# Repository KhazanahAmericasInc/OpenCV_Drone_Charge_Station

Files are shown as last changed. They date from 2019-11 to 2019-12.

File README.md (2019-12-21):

## Description  
An intelligent landing pad that can detect a drone flying overhead and take control to autonomously land the drone and recharge it. In this case, I am using an inexpensive indoor drone flown manually by a person before the autonomous landing procedure takes over control. In a commercial application, the drone would use other sensors to fly autonomous missions before the landing. I am focusing on just the landing portion of the problem.  

## Video  
YouTube Demo Video: https://www.youtube.com/watch?v=vQnh8SQZ9hY  

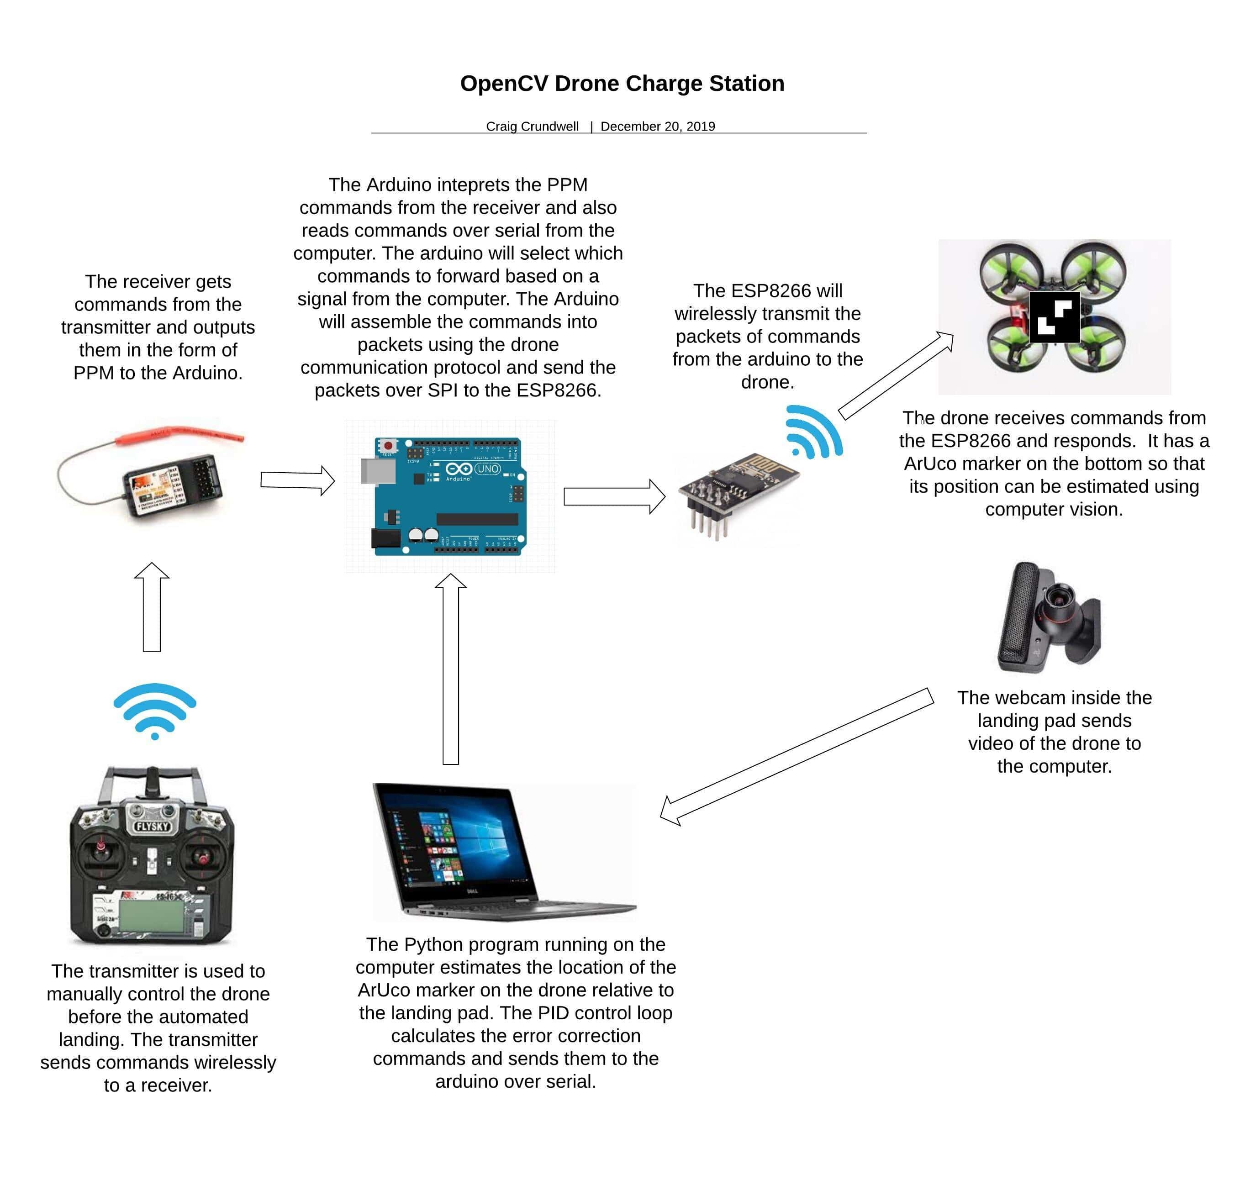
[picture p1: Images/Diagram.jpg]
Systems Diagram


To fly a drone autonomously, you need to know the actual location of the drone and a target location. Most advanced drones use GPS to accomplish this. For cheaper indoor drones, they have no sense of location so we need to provide this information to the control system.  We selected computer vision to track the drone position because it is inexpensive compared to other sensor options. The AruCo library is used to estimate the location of a small tag on the bottom of the drone. A webcam is located in the landing pad to view the drone flying above.  

Once we know the actual location of the drone and a desired location, we need to give the drone instructions to fly it autonomously. The system must calculate the appropriate commands to make the drone correct its position errors and try reach the target location. We can determine these commands using a PID control loop. A PID control loop has multiple values that can finely tune how the drone should respond to errors in it's location. The tuning of these values is critical for the drone to respond correctly without overshooting or causing other bad behavior like oscillations.  

For each axis of the drone's movement, there are 3 values to adjust; P, I, and D. The P value is proportional and represents how far the drone is from the target. If the drone is very far from the target, it must react strongly to bring it back to the target. The I value is integral and represents the past or historic error in the system. If the drone has been away from the target for a while, it must react strongly to try bring it back. D is for derivative and represents the current rate of change. If the drone is currently moving toward the target, less correction is required than if it is moving away from the target. PID values are different for every unique system. For example a more heavy and sluggish drone may need higher correction values to tune the flight vs a lighter and nimble drone. Even factors such as the frame rate of the camera will change the system response.  

In this project a Python program is used to read the video frames from the webcam and estimate the location of the drone. The program calculates the commands to send the drone to correct for errors when the drone drifts away from the target location. The Python program sends the commands over serial to a connected Arduino. The Arduino interprets these commands and assembles packets and transmits them to the drone using an Esp8266 module.  

Because we also need a way for the user to fly the drone before the landing pad takes control, there is a connected receiver to the Arduino that can forward commands from a user transmitter (controller). The Arduino can toggle between sending the commands from the computer, or commands from the users transmitter. This allows control of the drone to toggle between manual or autonomous flight.  

When the user flies the drone over the landing pad, the computer vision will detect the drone and the Python program tells the Arduino that it is taking over control. The Python program will set a target location and estimate the drone location. It will perform error calculations and send the drone commands to correct the position. When the Python program takes over control, the Arduino turns on the lights to allow the camera to more reliably track the drone location. The program hovers the drone for a few seconds to stabilize it before slowly lowering to the landing pad surface. Once the drone gets very close to the surface it experiences significantly increased lift called ground effect. The nearby ground increases the efficiency of the lift and causes the drone to bounce unless the throttle is dropped significantly. The PID loop is unable to handle this new system response so it fails to land the drone smoothly at this height. Instead, the throttle is lowered significantly for a short while before being turned off. This allows for a smoother landing.  

Once the drone has landed on the pad, it needs to doc with the charger. The drone is given gentle throttle and backward command so it slides backward and is physically guided into the charging dock. Magnets connect with small wires on the drone to transfer power and charge the battery.  

The Arduino can read the state of an LED on the charger which indicates if the it is still charging. The Arduino will fade the LED lights to indicate that the drone is charging. The charge is done when the lights turn off.  

When the charging is finished, the user can toggle a switch to make the landing pad physically disconnect the drone from the magnets and allow the drone to take off. The user performs the take off because it is difficult for an inexperienced user to take control of a drone already in flight. The reaction for adjusting the throttle must be very quick to prevent the drone from dropping of climbing too rapidly. Because of this, the computer has no problem reacting to taking control from a user smoothly but the reverse is challenging for the user.  

## Hardware
- Eachine E010 quadcopter 
- Arduino Uno 
- 2.4GHz nRF24L01+ 
- PlayStation Eye webcam  
- Flysky i6 transmitter 
- Flysky PPM compatible receiver  
- 12V power supply  
- 12V to 5V voltage converter 
- Windows 10 laptop

## Software
- Python 3.6 32bit  
- OpenCV contrib 4.1.2 
- Arduino 1.8.10
- CL Eye Driver 5.3.0.0341
- CL Eye Platform SDK 1.6.4.0028  

## Credit  
- Rotation matrix to euler angles math: https://www.learnopencv.com/rotation-matrix-to-euler-angles/   
- Inspiration and PID loop framework from @partomatl: https://github.com/partomatl   
- Signal filtering from @partomatl : https://github.com/partomatl   
- Transmitter protocol from goebish on RCgroups / github: https://github.com/goebish/nrf24_multipro  
- Serial communication modification of transmitter protocol from @perrytsao:  https://github.com/perrytsao  
- The PPM library @Nikkilae: https://github.com/Nikkilae/PPM-reader  

## TroubleShooting 
- A driver and SDK is required to run the play station camera on windows. The SDK package includes a test program which is useful to test the connection to the camera. Sometimes the camera needs to be moved to a different USB port and re selected in the test program to function properly. If the landing base does not react to the drone flying overhead, test the connection with the test program. 
- Avoid using the base with bright lights directly overhead as they can make it more difficult for the camera to detect the drone 
- Make sure the Aruco tracker on the bottom of the drone is not significantly bent or worn away. Replace it with a fresh one if required. 
- If the drone drifts a bit and does not fly level, the small trims buttons can be used to adjust for level flight  
- If the drone drifts significantly during flight, place it on a level surface and move both sticks to the bottom middle to re calibrate the on board sensors   
- If the system is drastically changed, the PID values may need to be tuned again. Start with the last known working values and adjust each P, I, or D value up or down slightly and monitor the system response. The pitch and roll can be tuned together if the system response is the same on both axis's (for a square drone it is usually the same). For common systems like the flight controller for a drone, the tuning process is well documented and online help can provide some rules of thumb to help speed up the process. For a less known system like this project the tuning is more guess and check. It is slow and frustrating but currently it is the only way.

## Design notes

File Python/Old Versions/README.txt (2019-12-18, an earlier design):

These programs were used to develop functinality. 
They are no longer compatabile with the the current arduino code versions

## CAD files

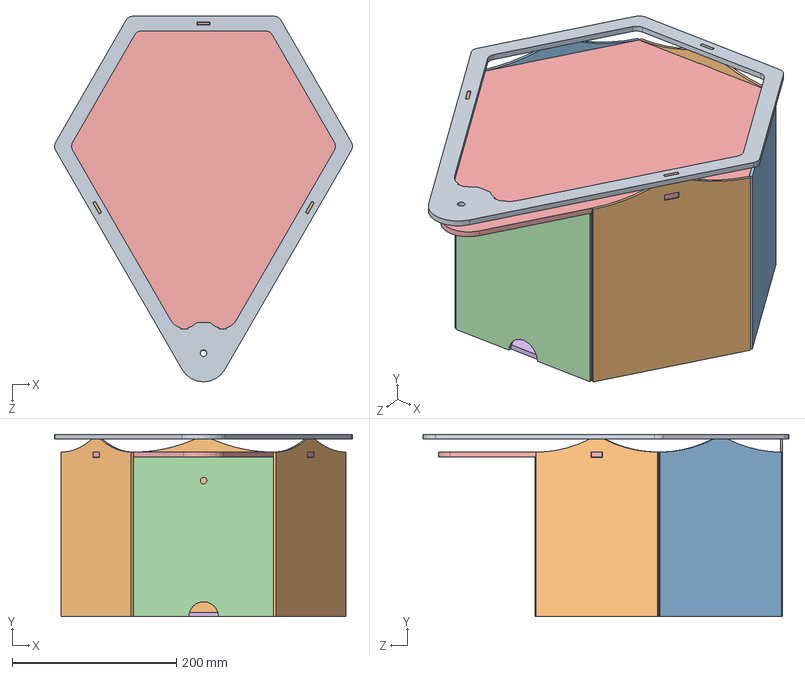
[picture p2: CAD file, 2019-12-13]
Solidworks/Hexagon base v1/Base_v1.SLDASM
362.5 x 221.5 x 444.9 mm
Top_v1
Side_v1 connect x 3
Side_v1 basic x 2
Side_v1 rear
pad_v1
Bottom_v1

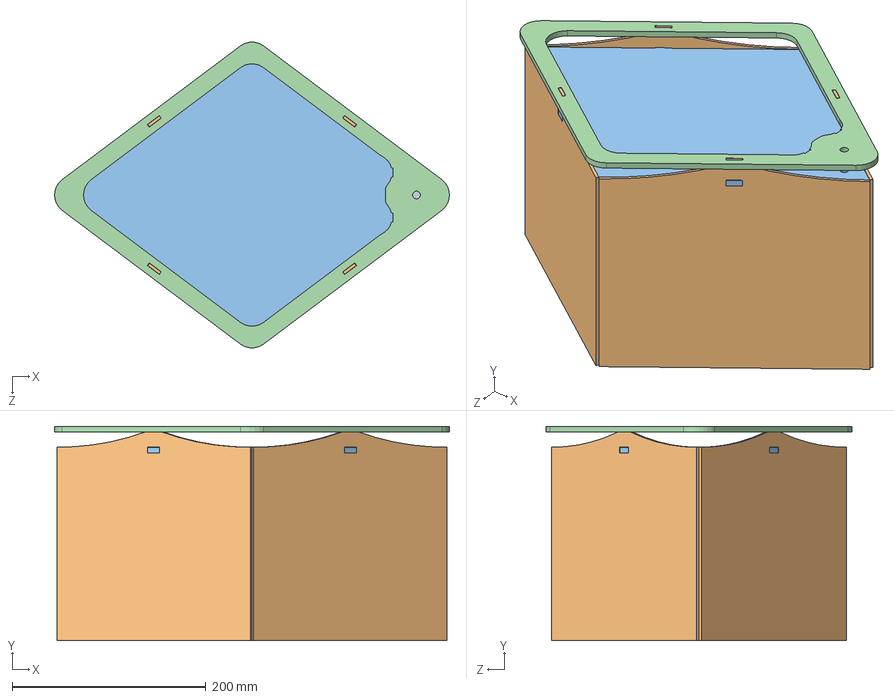
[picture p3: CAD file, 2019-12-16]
Solidworks/Diamond base v1/diamond_base_v1.SLDASM
408.2 x 221.5 x 315.9 mm
diamond_bottom_v1
diamond_side_v1 x 4
diamond_pad_v1
diamond_top_v1
diamond_middle_v1

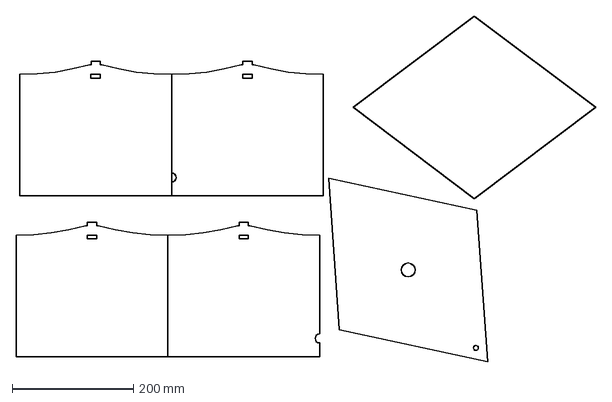
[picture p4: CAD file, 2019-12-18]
Solidworks/Diamond base v1/thin_black_cut_v1.dxf
954.8 x 568.7 mm

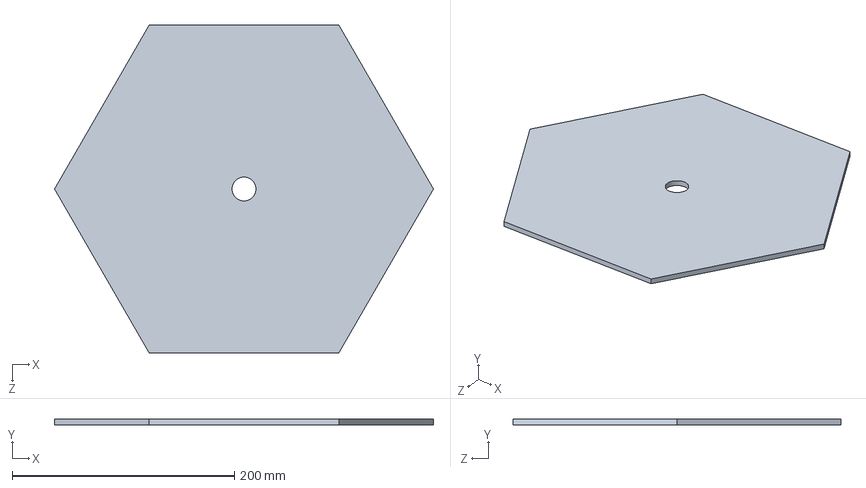
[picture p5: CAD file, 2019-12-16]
Solidworks/Hexagon base v1/middle_v1.SLDPRT
341.0 x 5.00 x 295.3 mm

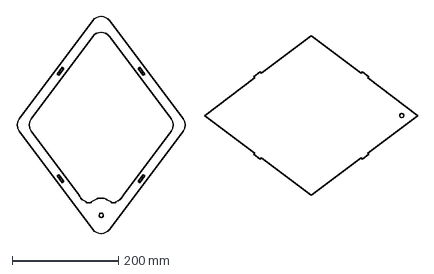
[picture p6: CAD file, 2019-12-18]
Solidworks/Diamond base v1/Thick_clear_cut_v1.dxf
754.3 x 408.3 mm

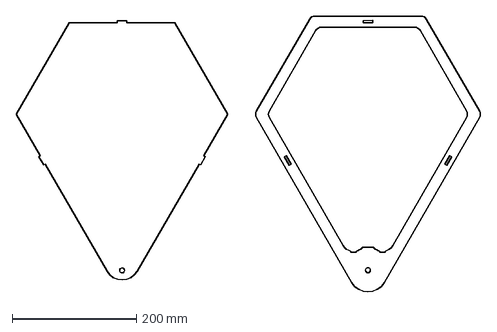
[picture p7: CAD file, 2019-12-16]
Solidworks/Hexagon base v1/Thick Clear Cut.dxf
748.7 x 444.9 mm

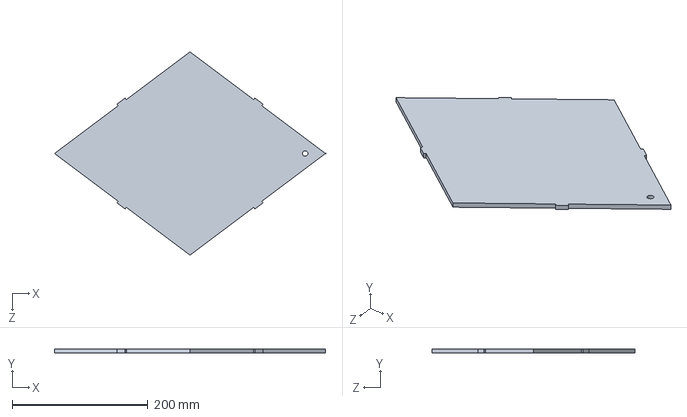
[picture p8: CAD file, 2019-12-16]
Solidworks/Diamond base v1/diamond_pad_v1.SLDPRT
400.0 x 5.63 x 300.0 mm

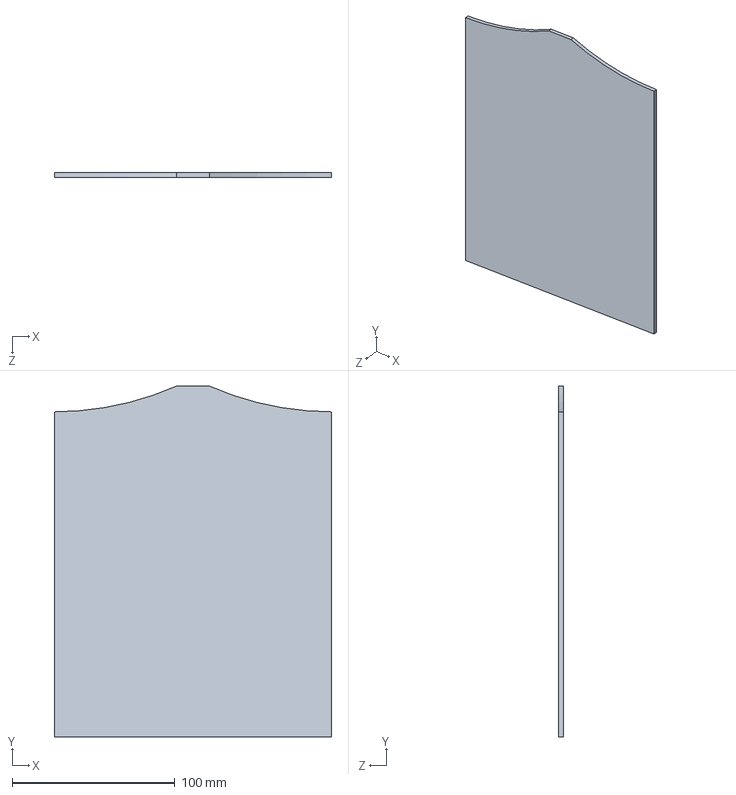
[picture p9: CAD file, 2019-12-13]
Solidworks/Hexagon base v1/Side_v1 basic.SLDPRT
170.5 x 215.9 x 2.95 mm

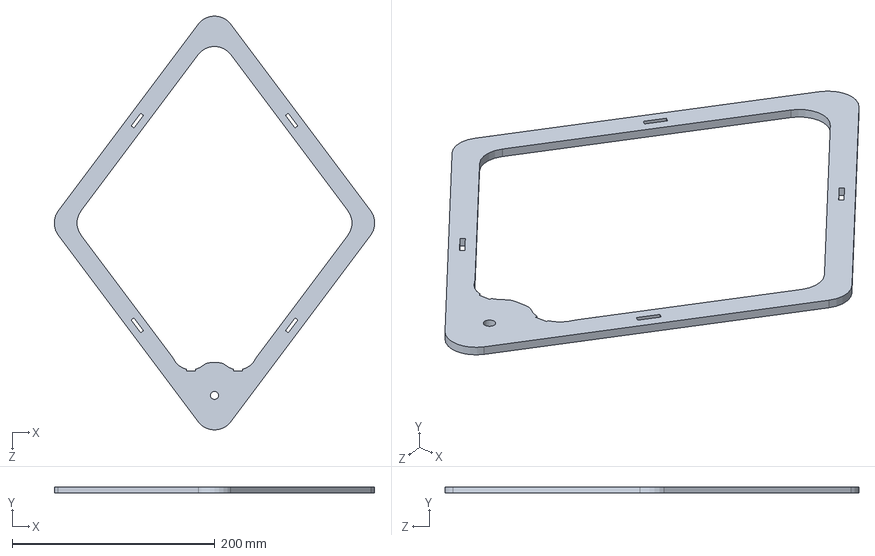
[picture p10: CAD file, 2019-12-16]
Solidworks/Diamond base v1/diamond_top_v1.SLDPRT
315.9 x 5.63 x 408.2 mm

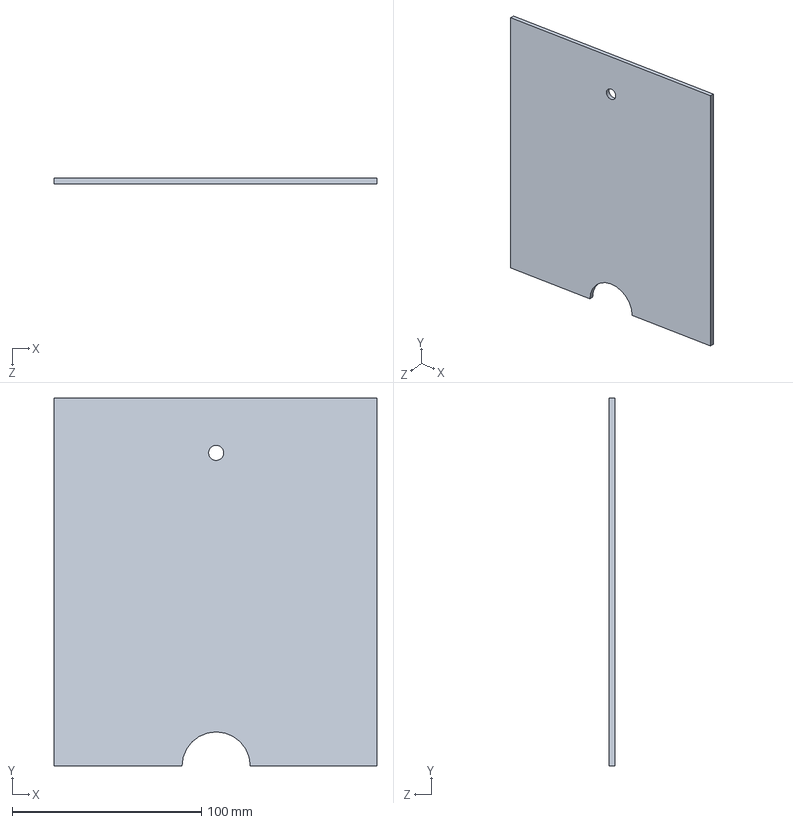
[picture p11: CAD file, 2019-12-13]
Solidworks/Hexagon base v1/Side_v1 rear.SLDPRT
170.5 x 194.3 x 2.95 mm

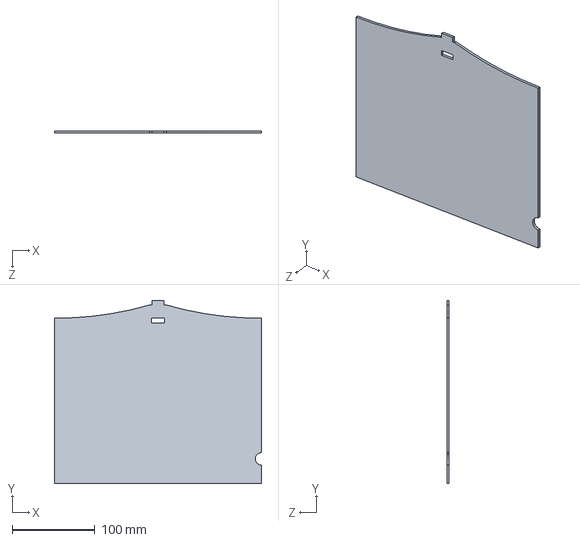
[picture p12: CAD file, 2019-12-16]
Solidworks/Diamond base v1/diamond_side_back_v1.SLDPRT
250.0 x 221.5 x 2.95 mm

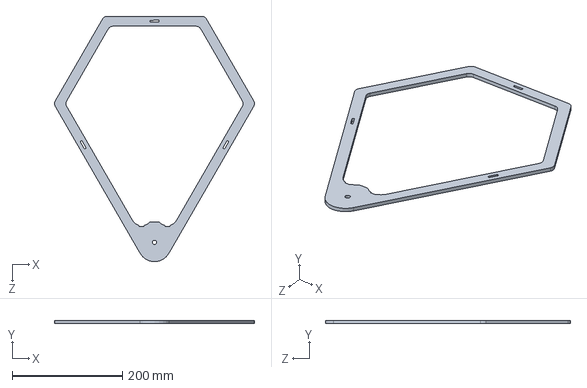
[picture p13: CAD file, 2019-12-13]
Solidworks/Hexagon base v1/Top_v1.SLDPRT
362.5 x 5.63 x 444.9 mm

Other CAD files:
Solidworks/Hexagon base v1/Thin Black Cut.dwg
Solidworks/Diamond base v1/diamond_middle_v1.SLDPRT
Solidworks/Hexagon base v1/Side_v1 connect.SLDPRT
Solidworks/Diamond base v1/diamond_bottom_v1.SLDPRT
Solidworks/Diamond base v1/diamond_side_v1.SLDPRT
Solidworks/Hexagon base v1/Bottom_v1.SLDPRT
Solidworks/Diamond base v1/Thick_clear_cut_v1.dwg
Solidworks/Diamond base v1/diamond_bottom_v1.DWG
Solidworks/Diamond base v1/diamond_middle_v1.DWG
Solidworks/Diamond base v1/diamond_pad_v1.DWG
Solidworks/Diamond base v1/diamond_side_back_v1.DWG
Solidworks/Diamond base v1/diamond_side_v1.DWG
Solidworks/Diamond base v1/diamond_top_v1.DWG
Solidworks/Diamond base v1/thin_black_cut_v1.dwg
Solidworks/Hexagon base v1/Bottom_v1.DWG
Solidworks/Hexagon base v1/Side_v1 basic.DWG
Solidworks/Hexagon base v1/Side_v1 connect.DWG
Solidworks/Hexagon base v1/Side_v1 rear.DWG
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

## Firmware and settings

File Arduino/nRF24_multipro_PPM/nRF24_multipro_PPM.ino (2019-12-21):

/*
 ******************************************************************************
 This is a fork of the Multi-Protocol nRF24L01 Tx project
 from goebish on RCgroups / github. 
 This serial communication of this program is from perrytsao on github.com
 The PPM library is from: https://github.com/Nikkilae/PPM-reader
 
 This version accepts either PPM or serial port strings and converts
 them to ppm commands which are then transmitted via
 the nRF24L01.
 The purpose of this code is to enable control over the Eachine E010 
 drone via code running on a PC or a FS-iA6B reciever connected via PPM. 

 This code reads channel values over serial from a Python program. 
 The first 4 channels are for control of the drone. The 5th channel selects 
 if the channel values from the python program should be sent to the drone 
 or if the channel values from the PPM of the attached receiver should be sent

 This code was tested on the Arduino Uno and nRF24L01 module.

 *********************************************************************************

 ##########################################
 #####   MultiProtocol nRF24L01 Tx   ######
 ##########################################
 #        by goebish on rcgroups          #
 #                                        #
 #   Parts of this project are derived    #
 #     from existing work, thanks to:     #
 #                                        #
 #   - PhracturedBlue for DeviationTX     #
 #   - victzh for XN297 emulation layer   #
 #   - Hasi for Arduino PPM decoder       #
 #   - hexfet, midelic, closedsink ...    #
 ##########################################


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
 You should have received a copy of the GNU General Public License.
 If not, see <http://www.gnu.org/licenses/>.
 */

#include <util/atomic.h>
#include <EEPROM.h>
#include "iface_nrf24l01.h"
#include <string.h>
#include <PPMReader.h>

//Used to control the servos
#include <Servo.h>

//PPM input on pin 2
int interruptPin = 2;

//Amount of channels to read from PPM
int channelAmount = 5;

//Initialize the ppm reader
PPMReader ppm(interruptPin, channelAmount);

int control = 1000;//Track control (1000 is user control, 2000 is computer control)
int triggerDetach = 0; //Toggle for charge detach
int lightMode = 0; //of for off, 1 for on, 3 for fade
int aux = 1000; //Used to record aux channel from user controller

//These values are used to average the voltage readings from the charger led
const int numReadings = 10;
int readings[numReadings];      // the readings from the analog input
int readIndex = 0;              // the index of the current reading
int total = 0;                  // the running total
int average = 0;                // the average

float brightness = 0;    // how bright the LED is
float fadeAmount = 0.3;    // how many points to fade the LED by

//Tracks timing of events
unsigned long lastString = 0;
unsigned long currentTime = 0;
unsigned long ElapsedTime = 0;

// ############ Wiring ################
//SPI Comm.pins with nRF24L01
#define MOSI_pin  3  // MOSI - D3
#define SCK_pin   4  // SCK  - D4
#define CE_pin    5  // CE   - D5
#define MISO_pin  A0 // MISO - A0
#define CS_pin    A1 // CS   - A1
#define landingLightPin 11 // the PWM pin the LED is attached to
#define ledPin    13 // LED  - D13
#define servoPin 6
#define chargePin A5

// SPI outputs
#define MOSI_on PORTD |= _BV(3)  // PD3
#define MOSI_off PORTD &= ~_BV(3)// PD3
#define SCK_on PORTD |= _BV(4)   // PD4
#define SCK_off PORTD &= ~_BV(4) // PD4
#define CE_on PORTD |= _BV(5)    // PD5
#define CE_off PORTD &= ~_BV(5)  // PD5
#define CS_on PORTC |= _BV(1)    // PC1
#define CS_off PORTC &= ~_BV(1)  // PC1
// SPI input
#define  MISO_on (PINC & _BV(0)) // PC0

#define RF_POWER TX_POWER_80mW

// PPM stream settings
#define CHANNELS 5 // number of channels in ppm stream, 12 ideally
enum chan_order{
    THROTTLE,
    AILERON,
    ELEVATOR,
    RUDDER,
    AUX1,  // (CH5)  led light, or 3 pos. rate on CX-10, H7, or inverted flight on H101
    AUX2,  // (CH6)  flip control
    AUX3,  // (CH7)  still camera (snapshot)
    AUX4,  // (CH8)  video camera
    AUX5,  // (CH9)  headless
    AUX6,  // (CH10) calibrate Y (V2x2), pitch trim (H7), RTH (Bayang, H20), 360deg flip mode (H8-3D, H22)
    AUX7,  // (CH11) calibrate X (V2x2), roll trim (H7)
    AUX8,  // (CH12) Reset / Rebind
};

//Define channel values 
#define PPM_MIN 1000
#define PPM_SAFE_THROTTLE 1050
#define PPM_MID 1500
#define PPM_MAX 2000
#define PPM_MIN_COMMAND 1300
#define PPM_MAX_COMMAND 1700
#define GET_FLAG(ch, mask) (ppm2[ch] > PPM_MAX_COMMAND ? mask : 0)
#define GET_FLAG_INV(ch, mask) (ppm2[ch] < PPM_MIN_COMMAND ? mask : 0)

// supported protocols
enum {
    PROTO_V2X2 = 0,     // WLToys V2x2, JXD JD38x, JD39x, JJRC H6C, Yizhan Tarantula X6 ...
    PROTO_CG023,        // EAchine CG023, CG032, 3D X4
    PROTO_CX10_BLUE,    // Cheerson CX-10 blue board, newer red board, CX-10A, CX-10C, Floureon FX-10, CX-Stars (todo: add DM007 variant)
    PROTO_CX10_GREEN,   // Cheerson CX-10 green board
    PROTO_H7,           // EAchine H7, MoonTop M99xx
    PROTO_BAYANG,       // EAchine H8(C) mini, H10, BayangToys X6, X7, X9, JJRC JJ850, Floureon H101
    PROTO_SYMAX5C1,     // Syma X5C-1 (not older X5C), X11, X11C, X12
    PROTO_YD829,        // YD-829, YD-829C, YD-822 ...
    PROTO_H8_3D,        // EAchine H8 mini 3D, JJRC H20, H22
    PROTO_MJX,          // MJX X600 (can be changed to Weilihua WLH08, X800 or H26D)
    PROTO_SYMAXOLD,     // Syma X5C, X2
    PROTO_HISKY,        // HiSky RXs, HFP80, HCP80/100, FBL70/80/90/100, FF120, HMX120, WLToys v933/944/955 ...
    PROTO_KN,           // KN (WLToys variant) V930/931/939/966/977/988
    PROTO_YD717,        // Cheerson CX-10 red (older version)/CX11/CX205/CX30, JXD389/390/391/393, SH6057/6043/6044/6046/6047, FY326Q7, WLToys v252 Pro/v343, XinXun X28/X30/X33/X39/X40
    PROTO_FQ777124,     // FQ777-124 pocket drone
    PROTO_E010,         // EAchine E010, NiHui NH-010, JJRC H36 mini
    PROTO_END
};

// EEPROM locationss
enum{
    ee_PROTOCOL_ID = 0,
    ee_TXID0,
    ee_TXID1,
    ee_TXID2,
    ee_TXID3
};

uint16_t overrun_cnt=0;
uint8_t transmitterID[4];
uint8_t current_protocol;
static volatile bool ppm_ok = false;
uint8_t packet[32];
static bool reset=true;
volatile uint16_t Servo_data[12];
static uint16_t ppm2[12] = {PPM_MIN,PPM_MID,PPM_MID,PPM_MID,PPM_MIN,PPM_MIN,
                           PPM_MIN,PPM_MID,PPM_MID,PPM_MID,PPM_MID,PPM_MID,};
                           
//Sets channels to safe values                          
int throttle = 1000;
int aileron, elevator, rudder = 1500;

String inputString = "";         // a string to hold incoming data
boolean stringComplete = false;  // whether the string is complete
char *p, *i;
char* c = new char[200 + 1]; // match 200 characters reserved for inputString later
char* errpt;
uint8_t ppm_cnt;

//Creates servo object
Servo servo;

void setup()
{
    
    randomSeed((analogRead(A4) & 0x1F) | (analogRead(A5) << 5));
    
    //Sets pinModes
    pinMode(servoPin, OUTPUT);
    pinMode(MOSI_pin, OUTPUT);
    pinMode(SCK_pin, OUTPUT);
    pinMode(CS_pin, OUTPUT);
    pinMode(CE_pin, OUTPUT);
    pinMode(MISO_pin, INPUT);

    TCCR1A = 0;  //reset timer1
    TCCR1B = 0;
    TCCR1B |= (1 << CS11);  //set timer1 to increment every 1 us @ 8MHz, 0.5 us @16MHz
    set_txid(false);

    // Serial port input/output setup
    Serial.begin(115200);
    
    // reserve 200 bytes for the inputString:
    inputString.reserve(200);

    //Attach servo and set it to a safe position
    servo.attach(servoPin);
    servo.write(0);
    delay(400);
    servo.detach(); //Detach prevents jitter when it is not in use

    //Initializes reading values to 0
    for (int thisReading = 0; thisReading < numReadings; thisReading++) {
    readings[thisReading] = 0;
    }
}

void loop()
{
    
    // reset / rebind
    uint32_t timeout=0;
    if(reset || ppm2[AUX8] > PPM_MAX_COMMAND) {
        reset = false;
        Serial.println("selecting protocol");
        selectProtocol();
        Serial.println("selected protocol.");
        NRF24L01_Reset();
        Serial.println("nrf24l01 reset.");
        NRF24L01_Initialize();
        Serial.println("nrf24l01 init.");
        init_protocol();
        Serial.println("init protocol complete.");
    }
    
    // process protocol
    switch(current_protocol) {
        case PROTO_E010:
            timeout = process_MJX();
            break;     
    }
    
    overrun_cnt=0;

    //Track timing 
    currentTime = millis();
    
    if (stringComplete) {
        // process string

       //record timing of string received 
       lastString = millis();
        
       strcpy(c, inputString.c_str());
       p = strtok_r(c,",",&i); // returns substring up to first "," delimiter
       ppm_cnt=0;
       while (p !=0){
         int val=strtol(p, &errpt, 10);
         if (!*errpt) {
           if (ppm_cnt == 4) //command #5 (cnt is 4) is the control value
           {
              control = val;
           }  
           else
           {
              //Record commands in array
              ppm2[ppm_cnt]=val;
           }
           
           }
           p = strtok_r(NULL,",",&i);
           ppm_cnt+=1;
         }

 
         // clear the string:
         inputString = "";
         stringComplete = false;
     }

     // Read the string from the serial buffer
     while (Serial.available()) {
       // get the new byte:
       char inChar = (char)Serial.read();
       // if the incoming character is a newline, set a flag
       // so the main loop can do something about it:
       if (inChar == '\n') {
         stringComplete = true;
       }
       else {
         // add it to the inputString:
         inputString += inChar;
       }
     }
     
    if (control == 1000) //Overwrite serial channels with signal from PPM
    {     
        
        lightMode = 0; //Light off
        ppm2[0] = ppm.latestValidChannelValue(3, 0);
        ppm2[1] = ppm.latestValidChannelValue(1, 0);
        ppm2[2] = ppm.latestValidChannelValue(2, 0);
        ppm2[3] = ppm.latestValidChannelValue(4, 0);
        aux = ppm.latestValidChannelValue(5, 0);
        servo.attach(servoPin); //Attach servo to be used by the user
    }

    if (control == 2000) //Accept serial channels 
    {
      lightMode = 1; //Light on
      servo.detach(); //Detach servo to prevent jitter
    }
    
    //Set aux channels to middle levels to keep flip and headless modes off
    ppm2[4] = 1500;
    ppm2[5] = 1500;

    //Calculate time since last string is received 
    ElapsedTime = currentTime - lastString;

    //If connection is lost with the python program, send safe commands to the drone 
    if (ElapsedTime >= 500)
    {
      ppm2[0] = 1000;
      ppm2[1] = 1500;
      ppm2[2] = 1500;
      ppm2[3] = 1500;
    }

    // subtract the last reading:
    total = total - readings[readIndex];
    // read from the sensor:
    readings[readIndex] = analogRead(chargePin);
    // add the reading to the total:
    total = total + readings[readIndex];
    // advance to the next position in the array:
    readIndex = readIndex + 1;
  
    // if we're at the end of the array...
    if (readIndex >= numReadings) {
      // ...wrap around to the beginning:
      readIndex = 0;
    }

    // calculate the average:
    average = total / numReadings;

    //If user toggles the aux 5 switch, move the servo
    if ((triggerDetach == 0) && (aux <= 1500))
    {
      ppm2[0] = 1000;
      servo.write(120);
      triggerDetach = 1; 
    }

    //If user toggles the aux 5 switch, move the servo
    if ((control==1000) && (triggerDetach == 1) && (aux >= 1500))
    {
      servo.write(0);
      triggerDetach = 0;
    }

    //If charging is detected, fade the leds
    if (average >= 800)
    {
      lightMode = 3; 
    }

    //Turn off leds
    if (lightMode == 0)
    {
      analogWrite(landingLightPin, 0);
    }

    //Turn on leds
    else if (lightMode == 1)
    {
      analogWrite(landingLightPin, 255);
    }

    //Fade leds
    else if (lightMode == 3)
    {
      // change the brightness for next time through the loop:
      brightness = brightness + fadeAmount;
  
      // reverse the direction of the fading at the ends of the fade:
      if (brightness <= 0 || brightness >= 150) {
        fadeAmount = -fadeAmount;
        }

      analogWrite(landingLightPin, (int)brightness); //Write value to led in
    }
       
    // wait before sending next packet
    while(micros() < timeout) // timeout for CX-10 blue = 6000microseconds.
    {
      // overrun_cnt+=1;
      };
}

//Sets the transmitter ID
void set_txid(bool renew)
{
    uint8_t i;
    for(i=0; i<4; i++)
        transmitterID[i] = EEPROM.read(ee_TXID0+i);
    if(renew || (transmitterID[0]==0xFF && transmitterID[1]==0x0FF)) {
        for(i=0; i<4; i++) {
            transmitterID[i] = random() & 0xFF;
            EEPROM.update(ee_TXID0+i, transmitterID[i]);
        }
    }
}


//Selects the communication protocol
void selectProtocol()
{
    // Modified and commented out lines so that Cheerson CX-10 Blue is always selected
    // wait for multiple complete ppm frames
    ppm_ok = false;

    current_protocol = PROTO_E010; // EAchine E010, NiHui NH-010, JJRC H36 mini
    
    // update eeprom
    EEPROM.update(ee_PROTOCOL_ID, current_protocol);
    // wait for safe throttle
}

//Initializes the communication protocol
void init_protocol()
{
    switch(current_protocol) {
        case PROTO_E010:
            MJX_init();
            MJX_bind();
            break;
    }
}


      
      

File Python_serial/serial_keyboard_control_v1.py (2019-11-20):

import serial
import time, keyboard

def clamp(n, minn, maxn):
    if n < minn:
        return minn
    elif n > maxn:
        return maxn
    else:
        return n


throttle_rate=15
aileron_rate=400
elevator_rate=400
rudder_rate=300

# define middle PPM values that make the drone hover
throttle_middle = 1600  # up (+) and down (-)
aileron_middle = 1500  # left (-) and right (+)
elevator_middle = 1500  # forward (+) and backward (-)
rudder_middle = 1500  # yaw left (-) and yaw right (+)

# define engines off PPM value for throttle
throttle_off = 999

arduino=serial.Serial('COM5', 115200, timeout=.01)

# wait a bit for the connection to settle
time.sleep(2)


throttle = throttle_off
aileron = aileron_middle
elevator = elevator_middle
rudder = rudder_middle

while (1):
    
    aileron = aileron_middle
    elevator = elevator_middle
    rudder = rudder_middle

    if keyboard.is_pressed('esc'): #ESC
        break
    
    if keyboard.is_pressed('w'): #throttle up
        throttle += throttle_rate

    elif keyboard.is_pressed('s'): #throttle down
        throttle -= throttle_rate

    if keyboard.is_pressed('a'): #yaw left
        rudder -= rudder_rate

    if keyboard.is_pressed('d'): #yaw right
        rudder += rudder_rate

    if keyboard.is_pressed('right'): #roll right
        aileron += aileron_rate

    if keyboard.is_pressed('left'): #roll left
        aileron -= aileron_rate
    
    if keyboard.is_pressed('up'): #pitch forward
        elevator += elevator_rate

    if keyboard.is_pressed('down'): #pitch back
        elevator -= elevator_rate

        

    throttle = clamp (throttle, throttle_off, 2000)
    aileron = clamp (aileron, 1000, 2000)
    elevator = clamp (elevator, 1000, 2000)
    rudder = clamp (rudder, 1000, 2000)

    
    command = "%i,%i,%i,%i" % (throttle, aileron, elevator, rudder) 
    command = command + "\n"
    arduino.write(command.encode())

    print("%i,%i,%i,%i" % (throttle, aileron, elevator, rudder))



command = "%i,%i,%i,%i" % (throttle_off, aileron_middle, elevator_middle, rudder_middle) 
command = command + "\n"
arduino.write(command.encode())

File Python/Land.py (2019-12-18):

#The goal of this project is to use computer vision to take control of a 
#   drone in flight and autonomously land and charge it

#This python program connects to an Arduino which handles the communication to the drone
#Please see the gitHub documentation for further information

#Credit:
#Rotation matrix to euler angles math: https://www.learnopencv.com/rotation-matrix-to-euler-angles/
#Inspiration and PID loop framework from @partomatl: https://github.com/partomatl
#Signal filtering from @partomatl


#Imports
import numpy as np
import cv2
import cv2.aruco as aruco
import sys, time, math
import serial
from scipy.signal import butter, lfilter
import keyboard


#Position Targets
xTarget = 0
yTarget = 0
zTarget = 50.0 #Note the zTarget is written over when the drone is first detected
angleTarget = 0

#Define a zone that the drone can be detected in
XYtransitionBoundry = 10
ZtransitionMax = 80
ZtransitionMin = 35

#Height where the prop wash of the drone causes instability and the PID
#   error loops falls apart. At this height the drone drops with dropThrottle
groundEffectHeight = 20
dropThrottle = 1575

#Keeps track of frames the drone is detected in
detectionCount = 0
detectionThreshold = 8
detectionLostThreshold = 70

#These are landing phases
phase0Timer = 8 #Hover
phase2Timer = 0.3 #Drop through prop wash zone
phase3Timer = 1 #Cut throttle and wait
phase4Timer = 3 #Slide backwards to dock
phase5Timer = 2 #Stop throttle

#Offset based on how the tag is placed on the drone
angleOffset = 315

#Velocity of decent
velocity = 0.15

#Define Aruco tag
id_to_find  = 42
marker_size  = 3 #This is in cm

#USB port for the Arduino serial
usb_port = 'COM15'

# define middle PPM values that make the drone hover
throttle_middle = 1690  # up (+) and down (-)
aileron_middle = 1500  # left (-) and right (+)
elevator_middle = 1500  # forward (+) and backward (-)
rudder_middle = 1500  # yaw left (-) and yaw right (+)

# motors off PPM value for throttle
throttle_off = 1000

#Set throttle to safe value while things settle
throttle = throttle_off

#Control channel selects computer or PPM control (from rc reciever on arduino pin 2)
#   1000 for user control (PPM) or 2000 for computer control 
control = 1000


#------------------------------------------------------------------------------
#------- ROTATIONS https://www.learnopencv.com/rotation-matrix-to-euler-angles/
#------------------------------------------------------------------------------
# Checks if a matrix is a valid rotation matrix.
def isRotationMatrix(R):
    Rt = np.transpose(R)
    shouldBeIdentity = np.dot(Rt, R)
    I = np.identity(3, dtype=R.dtype)
    n = np.linalg.norm(I - shouldBeIdentity)
    return n < 1e-6


# Calculates rotation matrix to euler angles
# The result is the same as MATLAB except the order
# of the euler angles ( x and z are swapped ).
def rotationMatrixToEulerAngles(R):
    assert (isRotationMatrix(R))

    sy = math.sqrt(R[0, 0] * R[0, 0] + R[1, 0] * R[1, 0])

    singular = sy < 1e-6

    if not singular:
        x = math.atan2(R[2, 1], R[2, 2])
        y = math.atan2(-R[2, 0], sy)
        z = math.atan2(R[1, 0], R[0, 0])
    else:
        x = math.atan2(-R[1, 2], R[1, 1])
        y = math.atan2(-R[2, 0], sy)
        z = 0

    return np.array([x, y, z])

#----------------------------------------------------------------------------------


# Calculates the shortest error "distance" between the actual and target angle
def getAngleError(actual, target, oldError):
    
    difference = target - actual
    if (difference > 180):
        actual += 360
    if (difference < -180):
        actual -= 360
    difference = target - actual

    return difference

#Checks if the drone is inside the transition boundry so computer can take control from the user safely
def ifInTransitionBoundry():
    return (zDrone > ZtransitionMin and zDrone < ZtransitionMax and yDrone > -XYtransitionBoundry
            and yDrone < XYtransitionBoundry and xDrone > -XYtransitionBoundry and xDrone < XYtransitionBoundry)


# record values for filtering
timeRecord = []
xRecord = []
yRecord = []
zRecord = []
angleRecord = []

# define a clamping function
def clamp(n, minimum, maximum):
    return max(min(maximum, n), minimum)

# define a Butterworth filter to filter the measurements
# call y = lfilter(b, a, data) to filter the data signal
order = 2  # second order filter
fs = 60  # sampling frequency is around 60 Hz
nyq = 0.5 * fs
lowcut = 2  # cutoff frequency at 2 Hz
low = lowcut / nyq
b, a = butter(order, low, btype='low')

# initialize drone variables
xDrone, yDrone, zDrone, angleDrone = 0, 0, 0, 0

# initialize PID controller
xError, yError, zError, angleError = 0, 0, 0, 0
xErrorI, yErrorI, zErrorI, angleErrorI = 0, 0, 0, 0
xErrorD, yErrorD, zErrorD, angleErrorD = 0, 0, 0, 0
xError_old, yError_old, zError_old, angleError_old = 0, 0, 0, 0

# define PID gains
KPx, KPy, KPz, KPangle = 4, 4, 2, -3
KIx, KIy, KIz, KIangle = 0.02, 0.02, 0.04, 0
KDx, KDy, KDz, KDangle = 250, 250, 220, 10

# count frames without detecting the drone
framesWithoutDrone = 0

# open serial connection with Arduino
# baudrate of 115200
arduino = serial.Serial(usb_port, 115200, timeout=.01)

# wait a bit for the connection to settle
print ("Connecting Arduino")
time.sleep(2)

#--- Get the camera calibration path
calib_path  = ""
camera_matrix   = np.loadtxt(calib_path+'cameraMatrix_PS_EYE.txt', delimiter=',')
camera_distortion   = np.loadtxt(calib_path+'cameraDistortion_PS_EYE.txt', delimiter=',')

#--- 180 deg rotation matrix around the x axis
R_flip  = np.zeros((3,3), dtype=np.float32)
R_flip[0,0] = 1.0
R_flip[1,1] =-1.0
R_flip[2,2] =-1.0

#--- Define the aruco dictionary
aruco_dict  = aruco.getPredefinedDictionary(aruco.DICT_4X4_50)
parameters  = aruco.DetectorParameters_create()

#--- Capture the webcam video
cap = cv2.VideoCapture(0)

#-- Set the camera size as the one it was calibrated with
cap.set(cv2.CAP_PROP_FRAME_WIDTH, 640)
cap.set(cv2.CAP_PROP_FRAME_HEIGHT, 480)

cap.set(cv2.CAP_PROP_FPS, 120)

#-- Font for the text in the image
font = cv2.FONT_HERSHEY_PLAIN

# wait a bit for the connection to settle
print ("Starting video capture")
time.sleep(2)

#Time values used for timing tasks
now = time.perf_counter()
last = now
phase0Start = 0
phase2Start = 0
phase3Start = 0
phase4Start = 0
phase5Start = 0

#Tracks the phase of landing
landPhase = 0

#Tracks loops so debugging values can print out every 50 frames
printcount = 0

#Sets who has control 
autoControl = 0

print ("Ready")
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

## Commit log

2019-12-03 Yaw axis tuned
2019-12-04 PSEye camera working
2019-12-12 Hover 11 basic landing working
2019-12-13 Solidwork files added
    [Base_v1.SLDASM, Bottom_v1.SLDPRT, Side_v1 basic.DWG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]
2019-12-16 added diamond base design
    [Base_v1.SLDASM, Bottom_v1.SLDPRT, Side_v1 basic.DWG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]
2019-12-16 added DWG files
    [Bottom_v1.DWG, Thick Clear Cut.dxf, Thick_clear_cut_v1.dwg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]
2019-12-18 Improved code comments
    [Thick_clear_cut_v1.dwg, Thick_clear_cut_v1.dxf, thin_black_cut_v1.dxf]

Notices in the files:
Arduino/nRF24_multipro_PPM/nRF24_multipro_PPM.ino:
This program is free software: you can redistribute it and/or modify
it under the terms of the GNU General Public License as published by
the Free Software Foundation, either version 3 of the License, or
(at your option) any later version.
